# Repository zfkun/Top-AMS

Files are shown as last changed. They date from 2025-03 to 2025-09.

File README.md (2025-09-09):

# Top-AMS





## 简介
- 本项目还在施工中
- 写一些介绍
- 目前支持最多八个通道
## 指南
首先需要准备以下硬件
### 主控模块
- [合宙esp32C3](https://wiki.luatos.com/chips/esp32c3/board.html)
- [PCB版](https://oshwhub.com/eda_xnlouvih/top-ams-8-tong-dao)(如果你只需要双色,也可以考虑直接在面包板上接线)
<!-- - 电机芯片<br>之后放上PCB版的嘉立创链接以及电机芯片的具体型号  -->
-
  | 通道  | 前向GPIO | 后向GPIO |    备注     |
  | :---: | :------- | :------- | :---------: |
  | 通道1 | GPIO2    | GPIO3    |
  | 通道2 | GPIO10   | GPIO6    |
  | 通道3 | GPIO5    | GPIO4    |
  | 通道4 | GPIO8    | GPIO9    |
  | 通道5 | GPIO0    | GPIO1    |
  | 通道6 | GPIO20   | GPIO21   |
  | 通道7 | GPIO12   | GPIO13   | 和LED灯冲突 |
  | 通道8 | GPIO18   | GPIO19   |  和USB冲突  |

- 使用通道7前,需要在web界面触发一次电机运行,激活后会使原先的所有灯语控制失效,避免干扰电机运行
- typeC口如果是由会持续协商充电协议的充电器供电,或者使用espidf调试刷入等,GPIO18,19就会有电平变化<br>
  经典版带串口芯片的不会有这个问题
### 上下料模块
- 上下料模块有多种电机方案,这些方案只是硬件设计不同,在与主控的接线上没有不同
- [起源N20](hard/N20电机方案/README.md)
  - 项目最早的设计方案
- [TT电机](https://makerworld.com.cn/zh/models/1418429-gua-pei-topduo-se-da-yin-de-ttji-chu-ji-v2-0#profileId-1540158)
  - 使用成本更低的TT电机
- [N20D](https://makerworld.com.cn/zh/models/1464399-n20dian-ji-8tong-ji-chu-ji#profileId-1594882)
  - 成对N20电机设计,有适配A1龙门的支架

### 刷入固件
- [固件刷入教程](https://docs.espressif.com/projects/esp-test-tools/zh_CN/latest/esp32/production_stage/tools/flash_download_tool.html)
- 固件刷完要重启
### esp配网
- 使用微信小程序 **一键配网**
- 配网协议选择 **SmartConfig** 
- 填入Wifi信息配网
### 连接打印机MQTT
- 在路由器中查看esp32的ip,登入esp32的web管理页面
- MQTT密码为打印机局域网模式里的密码,**局域网模式开关不影响连接**,建议直接在机器的小屏幕上查看
- 设备序列号除了在机器上直接查看外,也可以在 BambuStudio-设备-固件更新-序列号 中查看
### 配置打印机gcode
- 将对应机型的Gcode加入到打印机换色Gocde前
  - 目前只有A1mini的,但是其他打印机原理上也完全通用,只用改下几个数字就好,欢迎加群测试  
- 打印机使用热床温度范围 **1~17** 与AMS传递通道信息,请避免设置这个范围内的热床温度
- 退料前的回抽参数会自动读取使用的耗材配置,可在耗材配置内更改
- 切片软件的冲刷体积配置也能正常生效
- 冲刷体积一部分流量会被用于进料,请自行测试合适的冲刷体积
### 开始打印前
- 需要先将待换料的料线推进至能在 **进料时间** 内进入热端的距离
- 目前默认设定为首层不会换色,需要确认热端内的通道就是要打印的第一个颜色

## 其他  
### 兼容性测试
- A1 mini 固件版本1.04.00
- 1.05固件加了鉴权,现不支持
### 讨论
- Q群:8820913⑨九,注明来意
### 配套设施
- [迷你三通](https://makerworld.com.cn/zh/models/1289990-3tong-mini-wu-xu-qi-dong-jie-tou-chao-si-hua#profileId-1383310)

### 代办
- web心跳机制
- web上料线名称和颜色的修改和保存功能
- 自动续料
    - 思路:默认会续当前通道的下一个通道的料,在切片时候就要注意好.软件架构上,维护一个长度为使用的通道数(通过是否是NC脚判断)的布尔向量,记忆当前通道是否被续料过,这个记忆状态会在本次打印任务结束后重置
- 异常处理
  - mqtt断开
    - mqtt状态的更新和灯语
  - 因为料线刚好没了,无法退线的的报错
- 更小白的固件刷入教程

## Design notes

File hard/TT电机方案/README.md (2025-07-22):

## 需要购买硬件
- 橡胶圈
  - 参数要求: 外径9mm,线径1.9mm

- tt电机
  - 参数要求: 1：48就行

## 打印要求
层高0.16
无支撑打印注意小零件需要添加裙边
3mf文件已经分好盘了有些零件极其容易炒面

## 代办
可能未来会精简一下大小把

- 切片软件推荐旧版本2.0.1.50bambustudio,或者orca切片
- 打印机固件务必01.04.00.00
- 嘉立创白嫖教程看群文件word
- 挤出机模型https://makerworld.com.cn/zh/models/1065213-top_amsji-chu-ji-dai-huan-chong-6tong-dao-duo-se-d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
- 立创pcb8通文件 （推荐）https://oshwhub.com/eda_xnlouvih/top-ams-8-tong-dao
- 立创pcb文件6通（旧）未来不更新了https://oshwhub.com/eda_xnlouvih/yba-ams
- b站教程【手搓ams top_ams安装教学】 https://www.bilibili.com/video/BV1MwEGzLEhJ/?share_source=copy_web&vd_source=9cc2b22c6f281762c6d01fb7d7d9b921
- 【腾讯文档】BOM
https://docs.qq.com/sheet/DV2Zob25PQUhtUk1H?tab=BB08J2

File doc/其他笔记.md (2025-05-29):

- 在小绿点没有亮起的情况下发送退料gcode会导致UB
- 拓竹目前在"暂停-退料"的过程中(单独暂停或者单独退料不会),暂停中的Z轴会越抬约高,目前的解决方法是在"暂停-退料"中间插一段Z轴运动
    -  ```
        M211 S \nM211 X1 Y1 Z1\nM1002 push_ref_mode\nG91 \nG1 Z-1.0 F900\nM1002 pop_ref_mode\nM211 R\n
        ```
- 打包二进制包
  - ```bash
    esptool.py --chip esp32c3 merge_bin -o 包名.bin @flash_args

    cd build
    esptool.py --chip esp32c3 merge_bin -o TopAMS.bin --flash_mode dio --flash_freq 80m --flash_size 4MB 0x0 bootloader/bootloader.bin 0x10000 Top-AMS.bin 0x8000 partition_table/partition-table.bin
    ```
  不知道什么时候需要的命令格式又变了
  ```bash
  python -m esptool --chip esp32c3 merge_bin -o TopAMS.bin --flash_mode dio --flash_freq 80m --flash_size 4MB 0x0 bootloader/bootloader.bin 0x10000 Top-AMS.bin 0x8000 partition_table/partition-table.bin

  python -m esptool --chip esp32c3 merge_bin -o Top-AMS.bin --flash_mode dio --flash_freq 80m --flash_size 4MB 0x0 build/bootloader/bootloader.bin 0x10000 build/Top-AMS.bin 0x8000 build/partition_table/partition-table.bin

  ```

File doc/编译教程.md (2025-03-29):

# 编译教程
可以使用 ESP-IDF 命令行或者 VScode 进行编译

## 使用ESP-IDF命令行编译
1. 参照 [乐鑫官方教程](https://docs.espressif.com/projects/esp-idf/zh_CN/stable/esp32c3/get-started/windows-setup.html) 安装好ESP-IDF
2. 使用ESP-IDF命令行进入项目目录,如:
    ```bash
    cd 项目目录\Top-AMS
    ```
3. 设置好目标芯片类型,如 **ESP32-C3** :
    ```bash
    idf.py set-target esp32c3
    ```
4. 参照 [sdkconfig配置](./sdkconfig配置.md) 进行menuconfig配置
    ```base
    idf.py menuconfig
    ```
    如果你的芯片就是 **ESP32-C3** ,项目里已经有配置好的 `sdkconfig` 文件,将 `sdkconfig_esp32C3` 改名为 `sdkconfig` 即可
5. 填写配置信息.将 `config_examle.hpp` 改为为 `config.hpp` ,并在用户配置区填写好你的硬件信息等
6. 编译项目
    ```bash
    idf.py build
    ```
    首次编译耗时会比较长
7. 连接设备并烧录
   ```bash
   idf.py -p PORT flash
   ```
   **PORT** 为设备管理器里看到的设备串口号,如 **COM3**
8. 调试设备
   ```bash
    idf.py -p PORT monitor
    ```
    设备运行后就可以在看到设备运行的调试信息  
    
## 使用VScode进行编译
1. 下载[VScode](https://code.visualstudio.com/download)
2. 安装EDF-IDF插件  
按下Ctrl+Shift+X调出扩展,搜索esp-idf并安装
3. 

也可以参考[视频教程](https://www.bilibili.com/video/BV1mm4y1P7y7)

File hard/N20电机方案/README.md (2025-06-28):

# AMS进退料模块说明
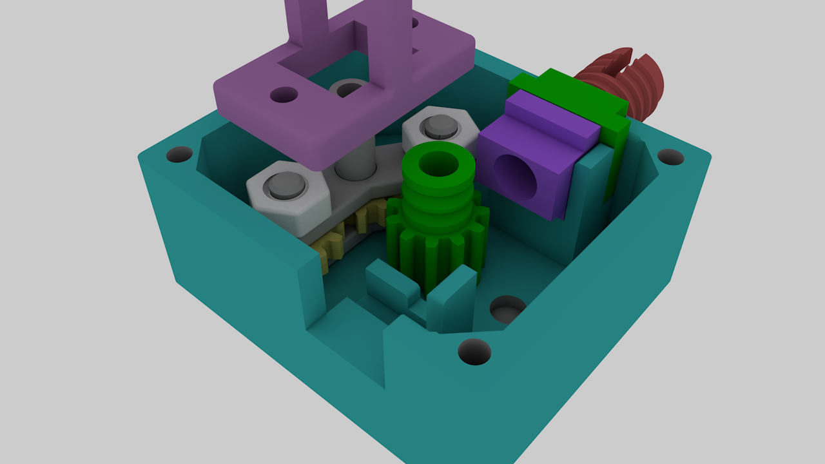
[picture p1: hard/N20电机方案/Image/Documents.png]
AMS渲染图


## 需要购买硬件
- 橡胶圈
  - 参数要求: 外径10mm,线径2.2mm
<!-- 
  - <a href="https://detail.tmall.com/item.htm?id=685184522549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" target="_blank">
    <img src="https://gw.alicdn.com/bao/uploaded/i1/2200743615196/O1CN01LUVTz31oFokhyCIq7_!!2200743615196.jpg_.webp" 
     alt="橡胶圈" width="300"  /> </a>
-->
- N20电机
  - 参数要求: 6V,60转/min,**额定力距1.5KB·cm**,轴长10mm
<!-- 
https://item.taobao.com/item.htm?id=525167243889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
-->
- 光轴
  - 参数要求: 直径4mm,长20mm
  - 打印也可以,需要打磨和确保精度
<!--
  https://detail.tmall.com/item.htm?id=680516964370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
-->
- M3螺丝

## 打印说明
- 个别零件太松太紧的,可以单独调节孔径补偿
- Z缝和拉丝需要打磨干净以保证顺滑度
- 伸入料线的时候,要确保进入两个橡胶轮中间,掰直料线避免捅歪

## 代办
- 支架设计,现在是双面胶

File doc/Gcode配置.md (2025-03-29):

### 配置说明
- 将对应机型的Gcode加入到打印机换色Gocde前  
- 打印机使用热床温度范围 **1~17** 与AMS传递通道信息,请避免设置这个范围内的热床温度
- 退料前的回抽参数会自动读取使用的耗材配置,可在耗材配置内更改
- 切片软件的冲刷体积配置也能正常生效

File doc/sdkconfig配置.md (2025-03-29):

# 正式编译烧录前的 SDK 配置说明
在开始编译和烧录之前，请按照以下步骤配置 `sdkconfig`:  
你可以在项目目录,使用**ESP-IDF命令行**运行
```bash
idf.py menuconfig
```
或使用VScode的 **SDK配置编辑器**

# 分区配置
进入 **Serial flasher config**:  
- 找到 **Flash size** 选项,设置为你的 Flash 大小,例如 `4MB`

进入 **Partiton Table** -> **Partition Table**  
- 选中 **Single factory app (large), no OTA**

# TLS配置  
进入 **Compoent config** -> **EPS-TLS** 并勾选
- **ESP-TLS Server: Set minimum Certificate Verification mode to Optional**(可能非必须)
- **Allow potentially insecure options**
- **Skip server certificate verification by default (WARNING: ONLY FOR TESTING PURPOSE, READ HELP)**

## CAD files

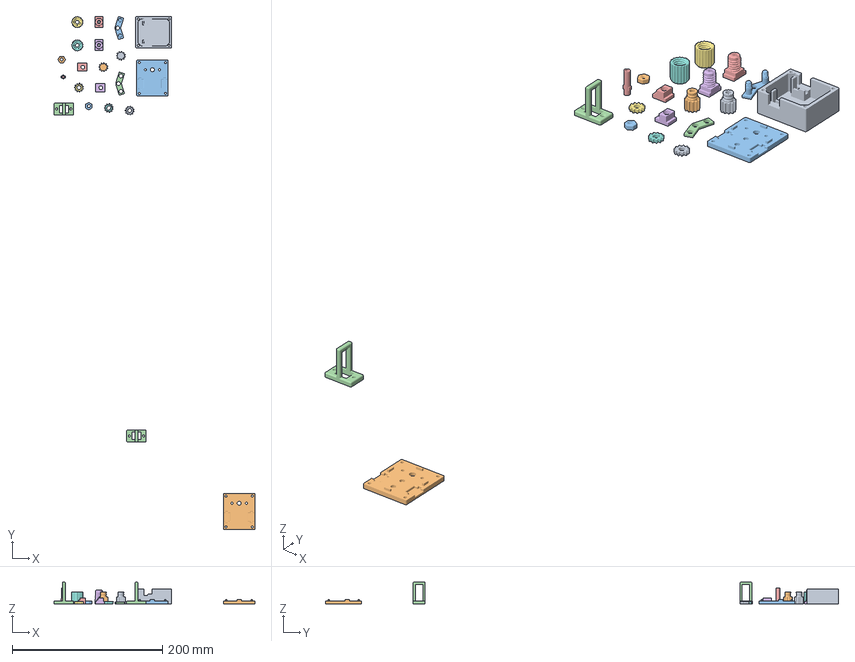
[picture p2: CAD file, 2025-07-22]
hard/N20电机方案/AMSV7.3.3mf
267.9 x 684.0 x 29.0 mm
盒体
盖子
滑动下层板
N20电机支架
料管模块 x 2
料管接口 x 2
橡胶轮 x 2
盖子(沉头螺丝
滑动上层板
料线模块L
料线模块R
从动轮 x 2
主动轮
R2螺栓 x 2
N20电机支架(沉头
马达轴传动

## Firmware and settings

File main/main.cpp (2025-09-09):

#include <Arduino.h>
#include <ArduinoJson.h>
#include <ESPAsyncWebServer.h>

#include "esptools.hpp"

#include "bambu.hpp"
#include "espIO.hpp"
#include "espMQTT.hpp"

#include "channel.hpp"

#include "esp_timer.h"

#include "web_sync.hpp"

#if __has_include("localconfig.hpp")
#include "localconfig.hpp"
#endif


using std::string;

//新添加的变量
TaskHandle_t Task1_handle;//微动任务
volatile int hw_switch = 0;
TaskHandle_t Task2_handle;//延时调试信息


//分割

int bed_target_temper_max = 0;
mesp::wsValue<std::string> ws_extruder("extruder", "1");//@_@先不存盘,也不给前端修改
std::atomic<int> extruder = 1;// 1-16,初始通道默认为1
int sequence_id = -1;
// std::atomic<int> print_error = 0;
std::atomic<int> ams_status = -1;
std::atomic<bool> pause_lock{false};// 暂停锁
std::atomic<int> nozzle_target_temper = -1;

//std::atomic<int> hw_switch{0};//小绿点, 其实是布尔

inline constexpr int 正常 = 0;
inline constexpr int 退料完成需要退线 = 260;
inline constexpr int 退料完成 = 0;// 同正常
inline constexpr int 进料检查 = 262;
inline constexpr int 进料冲刷 = 263;// 推测
inline constexpr int 进料完成 = 768;
//@_@应该放在一个枚举类里

AsyncWebServer server(80);
// AsyncWebSocket ws("/ws");
AsyncWebSocket& ws = mesp::ws_server;//先直接用全局的ws_server

inline mstd::channel_lock<std::function<void()>> async_channel;//异步任务通道

inline string last_ws_log = "日志初始化";//可能会有多个webfpr,非线程安全注意,现在单核先不管


//@brief WebSocket消息打印
inline void webfpr(AsyncWebSocket& ws, const string& str) {
    mstd::fpr("wsmsg: ", str);
    JsonDocument doc;
    doc["log"] = str;
    String msg;
    serializeJson(doc, msg);
    ws.textAll(msg);
    last_ws_log = str;
}

//@brief WebSocket消息打印
inline void webfpr(const string& str) {
    mstd::fpr("wsmsg: ", str);
    JsonDocument doc;
    doc["log"] = str;
    String msg;
    serializeJson(doc, msg);
    ws.textAll(msg);
    last_ws_log = str;
}

// @brief 控制电机运行(前向或后向)
// @param moter_id 电机编号,从 1 开始
// @param fwd 标识方向，true 表示前向，false 表示后向
// @param t 延时
template <typename T>
inline void motor_run(int motor_id, bool fwd, T&& t) {
    if (motor_id < 1 || motor_id > config::motors.size()) {
        webfpr(std::string("电机编号错误:") + std::to_string(motor_id));
        return;
    }
    motor_id--;
    if (config::motors[motor_id].forward == config::LED_R) [[unlikely]] {
        config::LED_R = GPIO_NUM_NC;
        config::LED_L = GPIO_NUM_NC;
    }//使用到了通道7,关闭代码中的LED控制
    if (fwd) {
        esp::gpio_out(config::motors[motor_id].forward, true);
        mstd::delay(std::forward<T>(t));// 使用传入的延时
        esp::gpio_out(config::motors[motor_id].forward, false);
    } else {
        esp::gpio_out(config::motors[motor_id].backward, true);
        mstd::delay(std::forward<T>(t));// 使用传入的延时
        esp::gpio_out(config::motors[motor_id].backward, false);
    }
}//motor_run

// @brief 获取有效的时间
// @param time_list 时间列表
// @param index 时间索引
// @param fallback 默认时间
template<typename T>
int get_valid_time(T* const* time_list, int index, int max, const T& fallback) {
    if (index >= 1 && index <= max) {
        int value = time_list[index - 1]->get_value();
        if (value > 0) {
            return value;
        }
    }

    return fallback.get_value();
}

// @brief 获取电机进料运转时间
// @param motor_id 电机的编号
inline int get_channel_load_time(int motor_id) {
    return get_valid_time(config::load_time_list.data(), motor_id, config::motors.size(), config::load_time);
}

// @brief 获取电机的退料运转时间
// @param motor_id 电机的编号
inline int get_channel_uload_time(int motor_id) {
    return get_valid_time(config::uload_time_list.data(), motor_id, config::motors.size(), config::uload_time);
}

// @brief 控制电机运行(前向或后向)
// @param moter_id 电机编号,从 1 开始
// @param fwd 标识方向，true 表示前向，false 表示后向
inline void motor_run(int motor_id, bool fwd) {
    motor_run(motor_id, fwd, fwd ? get_channel_load_time(motor_id) : get_channel_uload_time(motor_id));
}//motor_run





//@brief 发布消息到MQTT服务器
void publish(esp_mqtt_client_handle_t client, const std::string& msg) {
    esp::gpio_out(config::LED_L, true);
    // mstd::delay(2s);
    fpr("发送消息:", msg);
    int msg_id = esp_mqtt_client_publish(client, config::topic_publish().c_str(), msg.c_str(), msg.size(), 0, 0);
    //@_@这里的publish用到了topic_publish(默认),耦合了
    if (msg_id < 0)
        fpr("发送失败");
    else
        fpr("发送成功,消息id=", msg_id);
    // fpr(TAG, "binary sent with msg_id=%d", msg_id);
    esp::gpio_out(config::LED_L, false);
    // mstd::delay(2s);//@_@这些延时还可以调
    //我觉得延时还是加在程序里好调试
}




//换料
void change_filament(esp_mqtt_client_handle_t client, int old_extruder) {

    constexpr auto fpr = [](const string& r) { webfpr(ws, r); };//重设一下fpr

    fpr("开始换料");
    // esp::gpio_out(config::LED_R, false);
    if (config::load_time.get_value() <= 60000) {//这种区分可能不是很好@_@
        fpr("n20电机逻辑");
        int new_extruder = extruder;
        ws_extruder = std::to_string(old_extruder) + string(" → ") + std::to_string(new_extruder);

        publish(client, bambu::msg::runGcode("M211 S \nM211 X1 Y1 Z1\nM1002 push_ref_mode\nG91 \nG1 Z-5.0 F900\nM1002 pop_ref_mode\nM211 R\n"));//防止Z轴抬高
        fpr("防止Z抬高");

        publish(client, bambu::msg::uload);
        fpr("发送了退料命令,等待退料完成");
        mstd::atomic_wait_un(ams_status, 退料完成需要退线);
        fpr("退料完成,需要退线,等待退线完");

        motor_run(old_extruder, false);// 退线

        mstd::atomic_wait_un(ams_status, 退料完成);// 应该需要这个wait,打印机或者网络偶尔会卡

        publish(client, bambu::msg::runGcode("M109 S250\n"));
        while (nozzle_target_temper.load() < 245) {
            mstd::delay(500ms);// 等待热端温度达到250
        }
        // mstd::delay(5s);//先5s,时间可能取决于热端到250的速度,一个想法是把拉高热端提前能省点时间,但是比较难控制
        //@_@也可以读热端温度,不过如果读==250的话,肯定是挤出机先转,或者可以考虑条件为>240之类

        fpr("进线");
        publish(client, bambu::msg::runGcode("G1 E150 F500\n"));//旋转热端齿轮辅助进料
        mstd::delay(3s);//还是需要延迟,命令落实没这么快
        motor_run(new_extruder, true);// 进线

        extruder = new_extruder;//换料完成
        ws_extruder = std::to_string(new_extruder);// 更新前端显示的耗材编号

        // {//旧的使用进线程序的进料过程
        // 	publish(client,bambu::msg::load);
        // 	fpr("发送了料进线命令,等待进线完成");
        // 	mstd::atomic_wait_un(ams_status,262);
        // 	mstd::delay(2s);
        // 	publish(client,bambu::msg::click_done);
        // 	mstd::delay(2s);
        // 	mstd::atomic_wait_un(ams_status,263);
        // 	publish(client,bambu::msg::click_done);
        // 	mstd::atomic_wait_un(ams_status,进料完成);
        // 	mstd::delay(2s);
        // }

        publish(client, bambu::msg::print_resume);// 暂停恢复

        // mstd::delay(5s);// 等待命令落实,这个4s挺准
        // esp::gpio_out(config::motors[old_extruder - 1].forward, true);
        // mstd::delay(6s);// 辅助进料时间,@_@也可以考虑放在config
        // esp::gpio_out(config::motors[old_extruder - 1].forward, false);
        //前面辅助进料的话这里就不用了
    }

    else {
        fpr("tt电机逻辑");
        int new_extruder = extruder;
        fpr("退料中");
        ws_extruder = std::to_string(old_extruder) + string(" → ") + std::to_string(new_extruder);
        vTaskSuspend(Task1_handle);//关闭前进微动防止意外
        esp::gpio_out(config::motors[old_extruder - 1].backward, true);
        publish(client, bambu::msg::runGcode(std::string("M190 S") + std::to_string(bed_target_temper_max) + std::string("\nM211 S \nM211 X1 Y1 Z1\nG91 \nG1 Z-5.0 F900\nM211 R\nG1 E-20 F900\nM109 S250\n")));//恢复原来的热床温
        vTaskDelay(1000 / portTICK_PERIOD_MS);// 延迟1秒
        publish(client, bambu::msg::uload);
        vTaskDelay(1000 / portTICK_PERIOD_MS);// 延迟1秒
        esp::gpio_out(config::motors[old_extruder - 1].backward, false);
        mstd::atomic_wait_un(ams_status, 退料完成需要退线);

        motor_run(old_extruder, false);// 退线
        mstd::atomic_wait_un(ams_status, 退料完成);//应该需要这个wait,打印机或者网络偶尔会卡
        extruder = new_extruder;//换料完成
        ws_extruder = std::to_string(new_extruder);// 更新前端显示的耗材编号
        vTaskResume(Task1_handle);//恢复微动
        old_extruder = new_extruder;//切换新的通道
        publish(client, bambu::msg::runGcode(std::string("M109 S230")));

        fpr("进料中");
        esp::gpio_out(config::motors[old_extruder - 1].forward, true);

        for (size_t i = 0; i < 100; i++) {
            if (hw_switch == 1) {
                break;
            }

            vTaskDelay(1000 / portTICK_PERIOD_MS);//微动进料的时间可以自己改
        }

        esp::gpio_out(config::motors[old_extruder - 1].forward, false);


        if (hw_switch == 1) {
            webfpr("换料完成");
            publish(client, bambu::msg::print_resume);//继续打印
            esp::gpio_out(config::motors[old_extruder - 1].forward, true);
            mstd::delay(10s);

            esp::gpio_out(config::motors[old_extruder - 1].forward, false);
        } else
            fpr("卡料手动进");//这里出错处理没问题吗@_@


        fpr("换料结束");
        pause_lock = false;
    }
}// work
/*
 * 似乎外挂托盘的数据也能通过mqtt改动
 */


esp_mqtt_client_handle_t __client;

//上料
void load_filament(int new_extruder) {
    // __client;//先用这个,之后解耦出来,应该穿参进来,改好clien的生存期和错误回报就行

    if (!(new_extruder > 0 && new_extruder <= config::motors.size())) {
        webfpr("不支持的上料通道");
        return;
    }

    webfpr("开始进料");
    
    {//新写的N20上料
        publish(__client, bambu::msg::get_status);//查询小绿点
        mstd::delay(5s);//等待查询结果
        if (hw_switch == 1) {//有料需要退料
            int old_extruder = extruder;
            if (old_extruder == new_extruder) {
                webfpr("当前通道已经是" + std::to_string(new_extruder) + "无需上料");
                return;
            }
            ws_extruder = std::to_string(old_extruder) + string(" → ") + std::to_string(new_extruder);
            publish(__client, bambu::msg::uload);
            fpr("发送了退料命令,等待退料完成");
            mstd::atomic_wait_un(ams_status, 退料完成需要退线);
            fpr("退料完成,需要退线,等待退线完");

            motor_run(old_extruder, false);// 退线

            mstd::atomic_wait_un(ams_status, 退料完成);// 应该需要这个wait,打印机或者网络偶尔会卡
            webfpr("退线完成");
        }
        {//进料
            publish(__client, bambu::msg::runGcode("M109 S250\n"));
            while (nozzle_target_temper.load() < 245) {
                mstd::delay(500ms);// 等待热端温度达到250
            }
            // mstd::delay(5s);//先5s,时间可能取决于热端到250的速度,一个想法是把拉高热端提前能省点时间,但是比较难控制
            //@_@也可以读热端温度,不过如果读==250的话,肯定是挤出机先转,或者可以考虑条件为>240之类

            fpr("进线");
            publish(__client, bambu::msg::runGcode("G1 E150 F500\n"));//旋转热端齿轮辅助进料
            mstd::delay(3s);//还是需要延迟,命令落实没这么快
            motor_run(new_extruder, true);// 进线

            /*
            此处应该查下小绿点,如果小绿点没触发的话,G1命令无效
            */

            extruder = new_extruder;//换料完成
            ws_extruder = std::to_string(new_extruder);// 更新前端显示的耗材编号
            // publish(__client, 一段冲刷gcode,冲刷完后记得降温);@_@
        }
        webfpr("上料完成");
    }//新写的N20上料

    return;

    {//TT的上料
        publish(__client, bambu::msg::get_status);
        vTaskDelay(3000 / portTICK_PERIOD_MS);
        if (hw_switch == 0)//没有料所以直接进料
        {

            extruder = new_extruder;//修改为当前通道
            esp::gpio_out(config::motors[new_extruder - 1].forward, true);
            publish(__client, bambu::msg::load);

            for (size_t i = 0; i < 100; i++) {
                if (hw_switch == 1) {
                    break;
                }

                vTaskDelay(1000 / portTICK_PERIOD_MS);//微动进料的时间可以自己改
                webfpr("进料中");
            }
            if (hw_switch == 1) {
                esp::gpio_out(config::motors[new_extruder - 1].forward, false);

                int A = 0;
                for (size_t i = 0; i < 100; i++) {

                    if (ams_status == 262) {
                        if (A == 0) {
                            motor_run(new_extruder, true, 3s);// 进线
                            A = 1;
                        }

                        vTaskDelay(2000 / portTICK_PERIOD_MS);//微动进料的时间可以自己改
                        publish(__client, bambu::msg::click_done);
                    }
                    if (ams_status == 263) {
                        if (A == 1) {
                            motor_run(new_extruder, true, 3s);// 进线
                            A = 2;
                        }
                        vTaskDelay(2000 / portTICK_PERIOD_MS);//微动进料的时间可以自己改

                        publish(__client, bambu::msg::click_done);
                    }
                    if (ams_status == 进料完成) {
                        break;
                    }
                    vTaskDelay(2000 / portTICK_PERIOD_MS);//微动进料的时间可以自己改
                }



                publish(__client, bambu::msg::runGcode(std::string("M109 S200")));
                webfpr("换料成功");
                ws_extruder = std::to_string(new_extruder);// 更新前端显示的耗材编号

            } else {
                webfpr("卡料");
                esp::gpio_out(config::motors[new_extruder - 1].forward, false);
                ws_extruder = std::to_string(new_extruder);// 更新前端显示的耗材编号
                publish(__client, bambu::msg::runGcode(std::string("M109 S200")));
            }
        }

        else if (hw_switch == 1) {
            int old_extruder = extruder;

            publish(__client, bambu::msg::runGcode(std::string("M109 S250")));
            vTaskDelay(1000 / portTICK_PERIOD_MS);
            vTaskSuspend(Task1_handle);//关闭前进微动防止意外
            //减少压力
            publish(__client, bambu::msg::uload);
            webfpr("发送了退料命令,等待退料完成");
            esp::gpio_out(config::motors[old_extruder - 1].backward, true);
            mstd::delay(4s);
            esp::gpio_out(config::motors[old_extruder - 1].backward, false);

            mstd::atomic_wait_un(ams_status, 退料完成需要退线);
            webfpr("退料完成,需要退线,等待退线完");
            motor_run(old_extruder, false);// 退线
            mstd::atomic_wait_un(ams_status, 退料完成);//应该需要这个wait,打印机或者网络偶尔会卡
            vTaskResume(Task1_handle);//恢复微动
            extruder = new_extruder;//修改为当前通道
            esp::gpio_out(config::motors[new_extruder - 1].forward, true);
            publish(__client, bambu::msg::load);

            for (size_t i = 0; i < 100; i++) {
                if (hw_switch == 1) {
                    break;
                }

                vTaskDelay(1000 / portTICK_PERIOD_MS);//微动进料的时间可以自己改
                webfpr("进料中");
            }
            if (hw_switch == 1) {
                esp::gpio_out(config::motors[new_extruder - 1].forward, false);


                int A = 0;
                for (size_t i = 0; i < 100; i++) {

                    if (ams_status == 262) {
                        if (A == 0) {
                            motor_run(new_extruder, true, 3s);// 进线
                            A = 1;
                        }
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
extern "C" void app_main() {
#ifndef LOCAL_CONFIG
    for (size_t i = 0; i < config::motors.size() - 1; i++) {//-1是因为把8初始化了usb调试就没了
        auto& x = config::motors[i];
        esp::gpio_out(x.forward, false);
        esp::gpio_out(x.backward, false);
    }//初始化电机GPIO
#endif

    xTaskCreate(Task1, "Task1", 2048, NULL, 1, &Task1_handle);//微动任务
    xTaskCreate(Task2, "Task2", 2048, NULL, 1, &Task2_handle);//延时调试信息


    {// wifi连接部分
        mesp::ConfigStore wificonfig("wificonfig");

        string Wifi_ssid = wificonfig.get("Wifi_ssid", "");
        string Wifi_pass = wificonfig.get("Wifi_pass", "");

        if (Wifi_ssid == "") {
            WiFi.mode(WIFI_AP_STA);
            WiFi.beginSmartConfig();

            int cnt = 0;
            while (!WiFi.smartConfigDone()) {
                delay(1000);
                esp::gpio_out(config::LED_R, cnt % 2);
                ++cnt;
                fpr("Waiting for SmartConfig");
            }

            Wifi_ssid = WiFi.SSID().c_str();
            Wifi_pass = WiFi.psk().c_str();

            wificonfig.set("Wifi_ssid", Wifi_ssid);
            wificonfig.set("Wifi_pass", Wifi_pass);
        } else {
            WiFi.begin(Wifi_ssid.c_str(), Wifi_pass.c_str());
        }

        // 等待WiFi连接到路由器
        while (WiFi.status() != WL_CONNECTED) {
            delay(500);
            fpr("Waiting for WiFi Connected");
        }

        fpr("WiFi Connected to AP");
        fpr("IP Address: ", (int)WiFi.localIP()[0], ".", (int)WiFi.localIP()[1], ".", (int)WiFi.localIP()[2], ".", (int)WiFi.localIP()[3]);
        esp::gpio_out(config::LED_R, false);
    }// wifi连接部分

    // mesp::print_memory_info();

    // while (true) {
    //     mstd::delay(1000ms);
    // }

    using namespace config;
    using namespace ArduinoJson;
    using std::string;

    //异步任务处理,线程池
    std::thread async_thread([]() {
        while (true) {
            auto task = async_channel.pop();
            task();
        }
    });

    std::binary_semaphore mqtt_Signal{0};

    {//服务器配置部分
        server.on("/", HTTP_GET, [](AsyncWebServerRequest* request) {
            // request->send(200, "text/html", web.c_str());
            request->send(200, "text/html", web.data());
        });

        // 配置 WebSocket 事件处理
        ws.onEvent([&mqtt_Signal](AsyncWebSocket* server, AsyncWebSocketClient* client, AwsEventType type, void* arg, uint8_t* data, size_t len) {
            if (type == WS_EVT_CONNECT) {
                fpr("WebSocket 客户端", client->id(), "已连接\n");
                fpr(last_ws_log);
                webfpr(last_ws_log);

                JsonDocument doc;
                JsonObject root = doc.to<JsonObject>();
                root.createNestedArray("data");// 创建data数组

                for (auto& [name, to_json] : mesp::ws_value_to_json)
                    to_json(doc);// 添加当前值到data数组
                mesp::sendJson(doc);// 发送所有注册的值

                fpr(doc);
            } else if (type == WS_EVT_DISCONNECT) {
                fpr("WebSocket 客户端 ", client->id(), "已断开\n");
            } else if (type == WS_EVT_DATA) {// 处理接收到的数据
                fpr("收到ws数据");
                data[len] = 0;// 确保字符串终止

                JsonDocument doc;
                deserializeJson(doc, data);
                fpr("ws收到的json\n", doc, "\n");


                if (doc.containsKey("data") && doc["data"].is<JsonArray>()) {
                    for (JsonObject obj : doc["data"].as<JsonArray>()) {
                        if (obj.containsKey("name")) {
                            std::string name = obj["name"].as<std::string>();
                            auto it = mesp::ws_value_update.find(name);
                            if (it != mesp::ws_value_update.end()) {
                                it->second(obj);//更新值
                            }

                            if (name == "device_serial") {//需要连接mqtt,放这里感觉有些耦合
                                mqtt_Signal.release();
                            }
                        }
                    }
                }//wsvalue更新部分


                const std::string command = doc["action"]["command"] | string("_null");
                if (command != "_null") {//处理命令json
                    if (command == "motor_forward") {//电机前向控制
                        int motor_id = doc["action"]["value"] | -1;
                        async_channel.emplace(
                            [motor_id]() {
                                motor_run(motor_id, true);
                            });
                    } else if (command == "motor_backward") {//电机前向控制
                        int motor_id = doc["action"]["value"] | -1;
                        async_channel.emplace(
                            [motor_id]() {
                                motor_run(motor_id, false);
                            });
                    } else if (command == "load_filament") {
                        int new_extruder = doc["action"]["value"] | -1;
                        async_channel.emplace(
                            [new_extruder]() {
                                fpr("上料");
                                load_filament(new_extruder);
                            });

                    } else {
                        fpr("未知命令:", command);
                    }
                }//if command

            }//WS_EVT_DATA
        });
        server.addHandler(&ws);

        // 设置未找到路径的处理
        server.onNotFound([](AsyncWebServerRequest* request) {
            request->send(404, "text/plain", "404: Not found");
        });

        // 启动服务器
        server.begin();
        fpr("HTTP 服务器已启动");
    }


    {// 打印机Mqtt配置
        if (MQTT_pass != "") {// 有旧数据,可以先连MQTT
            fpr("当前MQTT配置\n", bambu_ip, '\n', MQTT_pass, '\n', device_serial);
            mesp::Mqttclient Mqtt(mqtt_server(bambu_ip), mqtt_username, MQTT_pass, callback_fun);
            webfpr(ws, "MQTT连接中...");
            Mqtt.wait();
            if (Mqtt.connected()) {
                auto temp = last_ws_log;
                webfpr("MQTT连接成功");
                last_ws_log = temp;//@_@或许应该改改webfpr,让它不覆盖
                MQTT_done = true;
                work(Mqtt);
            } else {
                MQTT_done = false;
                //Mqtt错误反馈分类
                webfpr(ws, "MQTT连接错误");
            }
        }//if (MQTT_pass != "")

        while (!MQTT_done) {
            fpr("等待Mqtt配置");
            mqtt_Signal.acquire();// 等待mqtt配置
            fpr("当前MQTT配置\n", bambu_ip, '\n', MQTT_pass, '\n', device_serial);
            mesp::Mqttclient Mqtt(mqtt_server(bambu_ip), mqtt_username, MQTT_pass, callback_fun);
            webfpr(ws, "MQTT连接中...");
            Mqtt.wait();
            if (Mqtt.connected()) {
                webfpr("MQTT连接成功");
                MQTT_done = true;
                work(Mqtt);
            } else {
                //Mqtt错误反馈分类
                MQTT_done = false;

                webfpr(ws, "MQTT连接错误");
            }
        }
    }



    int cnt = 0;
    while (true) {
        mstd::delay(20000ms);
        // esp::gpio_out(esp::LED_R, cnt % 2);
        ++cnt;
    }
    return;
}

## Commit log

2025-03-29 移动旧文件
2025-03-29 一些配置修改
2025-03-30 整理N20方案硬件说明
    [AMSV6.1.3mf]
2025-03-30 fix图片路径
2025-03-30 其他模块
2025-04-02 更新了config,可以存flash
2025-04-04 一些小说明
2025-04-05 加入网页中
2025-04-05 编写websocket中
2025-04-05 mqttweb配置完成,待测试
2025-04-06 Mqtt配置大体完成
2025-04-07 加了日志框
2025-04-08 重设电机管脚
2025-04-08 增到8个通道,增加说明
2025-05-08 写了些教程
2025-05-09 补充了教程
2025-05-15 去掉了ESPUI
2025-05-24 修改了web嵌入方式
2025-05-24 增加了readme说明
2025-05-25 改了mqtt配置的更新方式
2025-05-25 通道管理基础
2025-05-26 加了web控制电机
2025-05-28 加了进退料时间同步
2025-05-28 加微动缓冲和当前通道同步
2025-06-03 加了同步进料
2025-06-07 修改了下web部分
2025-06-07 优化了webUI
2025-06-07 fix web日志
2025-06-07 一些小更新
2025-06-10 加大了mqtt的缓存
2025-06-13 修复了任务分派
2025-06-14 1测试用的6通板子之后会把io口改回去2使用旧微动的程序
2025-06-14 callback里添加了每5次获取打印机完整状态防止丢包时卡顿 优化了微动触发
2025-06-14 1更新上料程序 2在config里添加了#define宏 在头文件里注释掉就是8通道 默认6通板子
2025-06-16 修复了切换通道有概率卡死的bug 添加了tt电机的逻辑只要进料时间大于1分钟就是tt电机的换料逻辑
2025-06-16 整理格式
2025-06-27 更新N20AMSV7
    [AMSV6.1.3mf, AMSV7.2.3mf]
2025-06-27 补充N20说明
2025-06-27 修改tt电机说明
2025-06-28 优化内存占用
2025-06-29 修补任务分配bug,写了N20上料
2025-06-29 加了些说明
2025-07-02 feat: 增加通道自定义进退料时间设置
2025-07-21 N20硬件更新到v7.3,加了沉头螺丝洞(可选)和料线限位,现在可以盲捅料线进去
    [AMSV7.2.3mf, AMSV7.3.3mf]
2025-07-29 修改说明
2025-08-07 增加了群友挤出机方案链接
2025-08-08 又改了一部分为string_view
2025-08-09 增加通道各个属性的同步
2025-08-11 修正了6通道gpio定义（测试中暂时先用6通道禁用初始化电机）
2025-08-18 增加检测与打印机连接超时直接显示在控制台
